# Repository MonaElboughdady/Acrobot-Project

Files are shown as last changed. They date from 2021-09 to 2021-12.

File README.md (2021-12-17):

# Acrobot-Project
The acrobot is a two-link robot manipulator ( it has three links if we counted the base) with only one actuator at the second joint. In this project I designed, and built an acrobot from scratch with the help of my supervisor. we didn't use any motion transfer methods (such as gears and timing belts with pulleys) in this hardware. It was also required to stablize it using LQR control in minimal and maximal coordinates. The mechanical design still needs some modifications for the controller to work in the upright position, but unfortunately I no longer have access to the hardware.  
single pendulum

## The mechanical design and hardware
The design is very simple and the links used are inexpensive and can be obtained easily.To connect the parts together, we designed connections and used 3D printing technology to maufacture them. We designed similar connections that can be produced using milling, but we didn't manufacture them.
### List of components 
this list contains all the mechanical and electronics components that we used (nX) means we used n parts. d = diameter, t= thickness
* Base link: it is a 20mm d X 1mm t X 205mm aluminum tube  https://www.bauhaus.info/metallprofile-kunststoffprofile/kantoflex-rundrohr/p/26683708 (The strength of the tube is good and enough for this application. However, I recommend getting a steel tube for a longer life cycle) 
* Bearings: (2X) 6004-ZZ with width 12mm, Inner diameter 20mm and outer diameter 42mm https://www.bauhaus.info/kugellager/kugellager-6004-zz/p/26538118( you can get other bearings with an inner diameter of 20 mm, but the dimensions of the housing needs to be changed)
* Link1: 1 mm t X 20x20mm X 300mm square Aluminum tube https://www.bauhaus.info/metallprofile-kunststoffprofile/kantoflex-vierkantrohr/p/10508571 
* Link2: it is a 20mm diam* 200mm aluminum tube with a 12mm d X 18 mm steel rod (I recommend getting a 20mm d X 1 mm t X 200mm steel tube or 20mm* 300mm aluminum rod) 
* Motor: Odrive DUAL SHAFT MOTOR D5065 270KV https://eu.odriverobotics.com/shop/odrive-custom-motor-d5065
* Motor driver: ODRIVE V3.6 56volts with connectors https://eu.odriverobotics.com/shop/odrive-v36 ( I may consider getting moteus r4.8 developer kit to build another acrobot but this will require some modifications in the design https://mjbots.com/products/moteus-r4-8-developer-kit )
* Microcontroller: Teensy4.1 development board https://www.conrad.com/p/pjrc-microcontroller-teensy-41-2269230 ( I don't recommend using Arduino microcontroller in this project. You can make it work with arduino however the control code will be more complicated and you will need to use native protocol instead of Ascii for UART communication)
* Encoders: (2X) Incremental capacitive encoder CUI AMT102-V https://eu.odriverobotics.com/shop/cui-amt-102 (I recommend getting absolute encoders as they will reduce the calculations)
* The base:  You can get any wooden or metal base, but you should make sure that it is stable and doesn't move while the acrobot is working)
## Modelling and control
* We used Julia programming language to write the Acrobot parameters, and calculated the LQR controller gains. We also tried to use Julia to control the Acrobot, but it is not a good idea.
(You can also use matlab or any language for calculations)
* We used Arduino IDE to write codes to the teensy. The instructions for installation can be found here https://www.pjrc.com/teensy/td_download.html. You can use both linux and windows operating systems for teensyarduino.
* We ran some experiments on the second actuated link while fixing the first link(simple pendulum). The teensy and Julia codes for the simple pendulum are included in this rep.
## Communication 
Since we need to send torque values to the odrive and receive the positions and velocities data from the odrive, we used UART communication and send the commands using ASCII protocol. More information about ASCII protocol can be found here https://docs.odriverobotics.com/ascii-protocol. I tried testing native protocol. Although it is faster than the ASCII, it is more complicated. You can find more info about the native protocol here https://docs.odriverobotics.com/native-protocol. I have posted my native protocol notes in https://github.com/MonaElboughdady/Acrobot-Project/tree/main/Calculations.

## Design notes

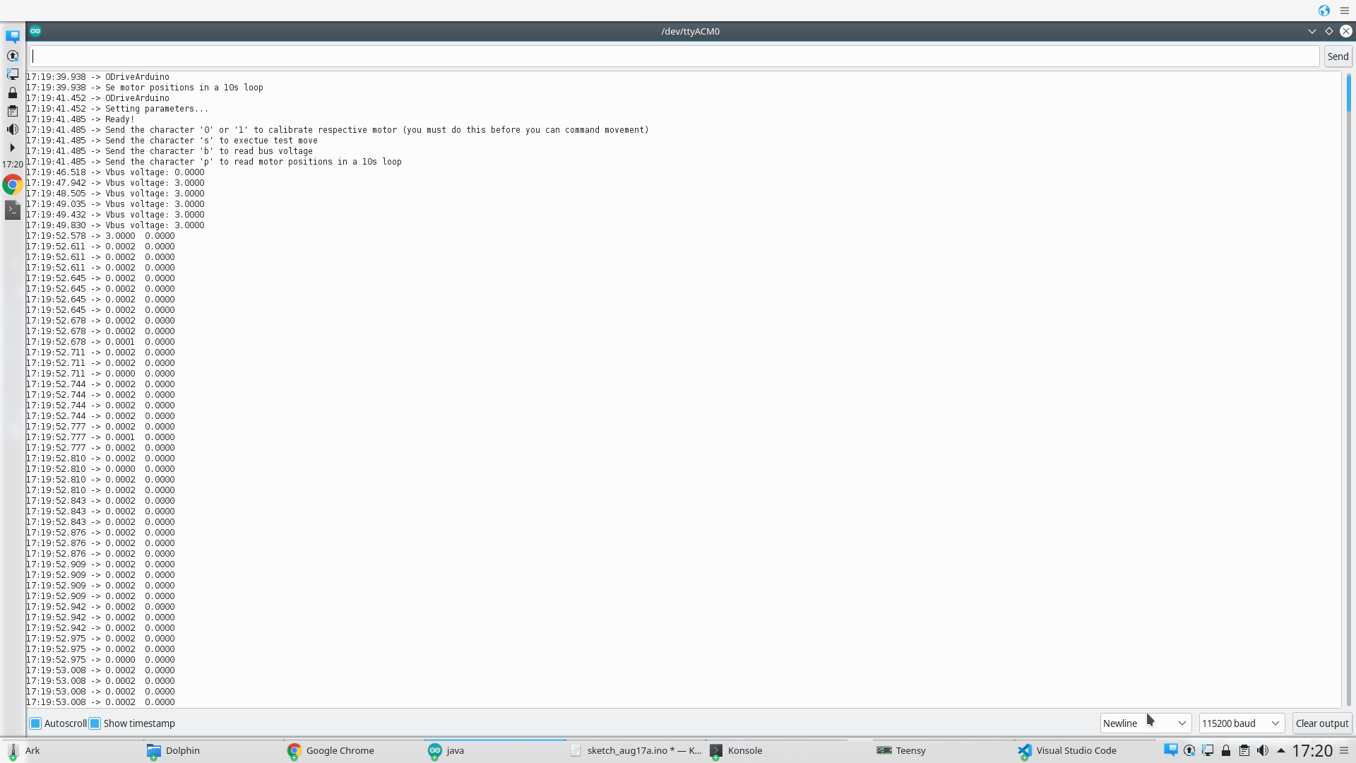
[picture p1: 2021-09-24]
Screenshot_20210924_172021.png

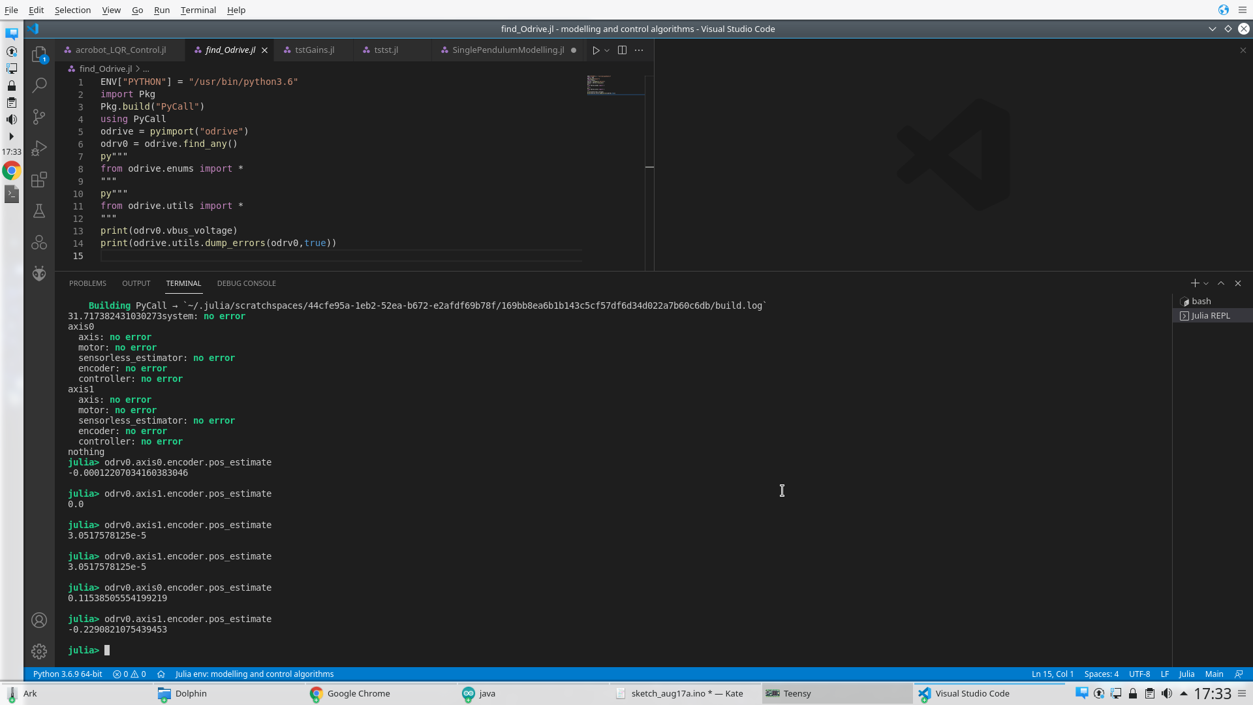
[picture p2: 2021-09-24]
Screenshot_20210924_173316.png

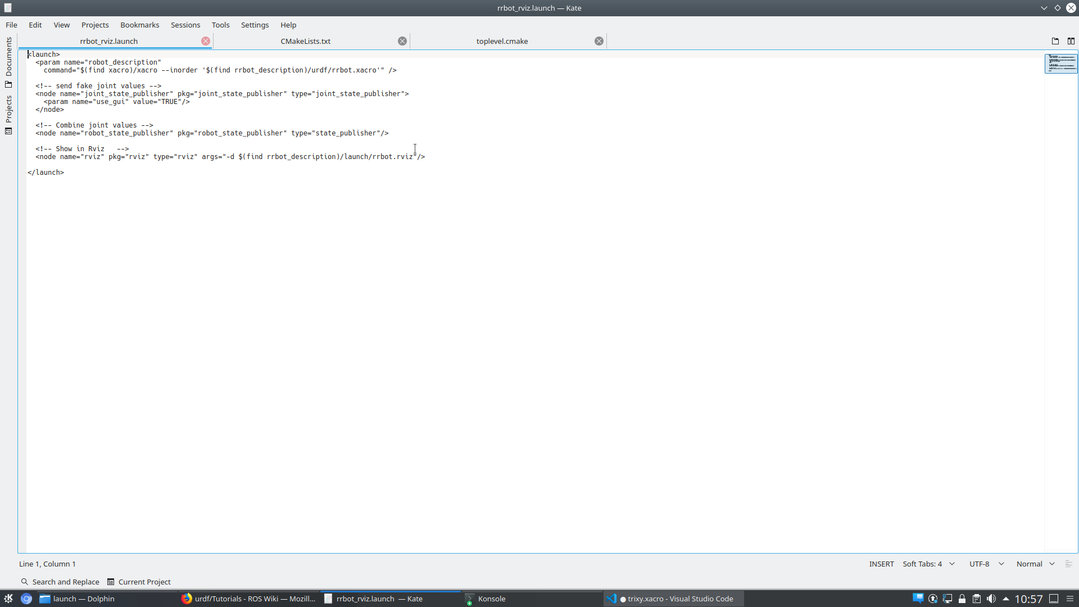
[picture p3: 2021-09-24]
Screenshot_20210520_105743.png

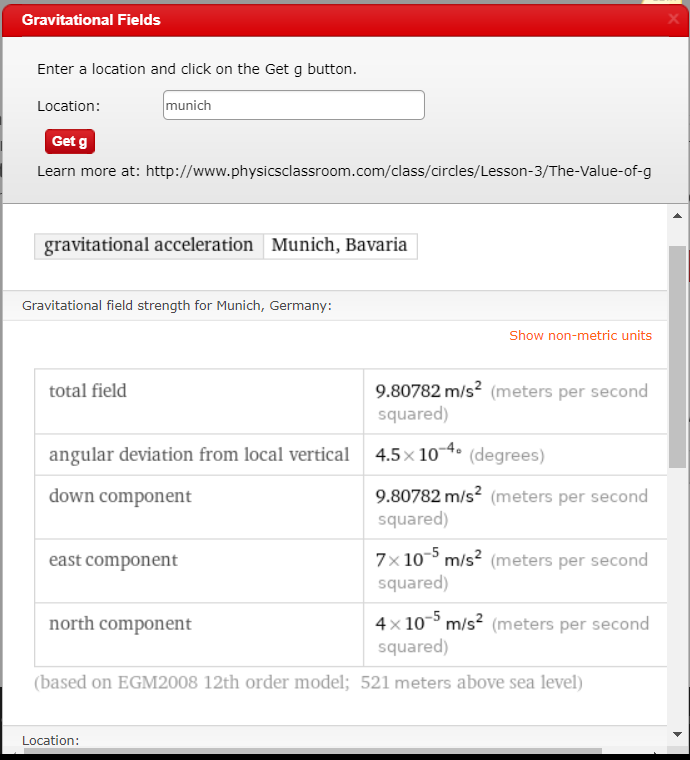
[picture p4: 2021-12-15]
Calculations/GravityInMunich.PNG

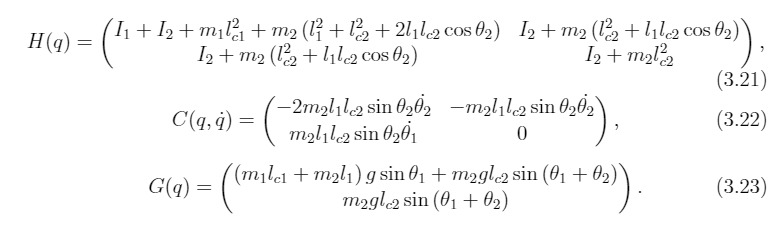
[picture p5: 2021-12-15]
Calculations/WhatsApp Image 2021-10-12 at 3.36.40 PM.jpeg

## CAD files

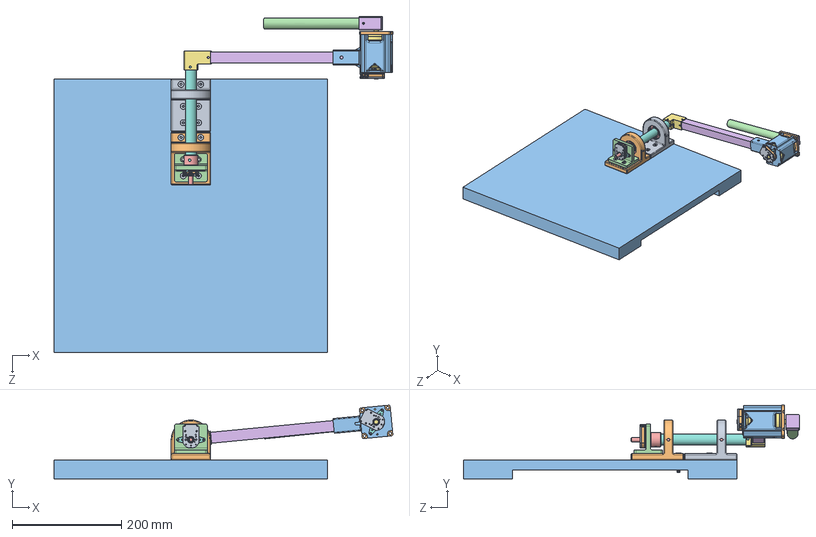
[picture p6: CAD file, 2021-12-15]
Design/Assem1.SLDASM
619.2 x 134.6 x 614.0 mm
base1_left
base1 (1)
enclosure2withrod
Lbracket
connector2
squareCsLink
Motr
amt102-v_01 x 2
amt102-v_02 x 2
amt102-v_03 x 2
amt102-v_04 x 2
amt102-v_05 x 2
amt102-v_06 x 2
amt102-v_07 x 2
amt102-v_08 x 2
amt102-v_09 x 2
amt102-v_10 x 2
amt102-v_11 x 2
amt102-v_12 x 2
amt102-v_13 x 2
amt102-v_14 x 2
amt102-v_15 x 2
AMT-B0-W x 2
hexa csunk highhd screw_iso x 10
enclosure1
woodenBase
Second Link
radial ball bearing_68_din x 2
connectionToRod2_mod
connector_to_base

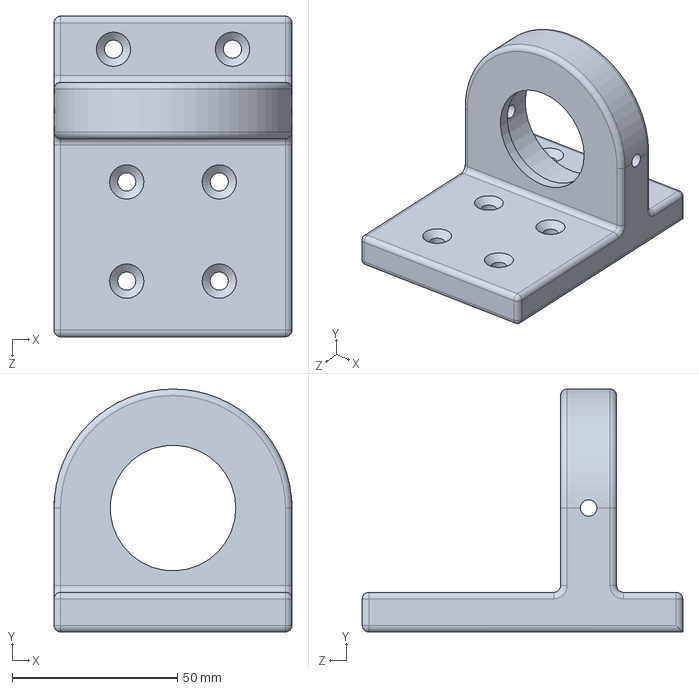
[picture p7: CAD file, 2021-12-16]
Design/base1_left.SLDPRT
72.0 x 73.5 x 97.0 mm

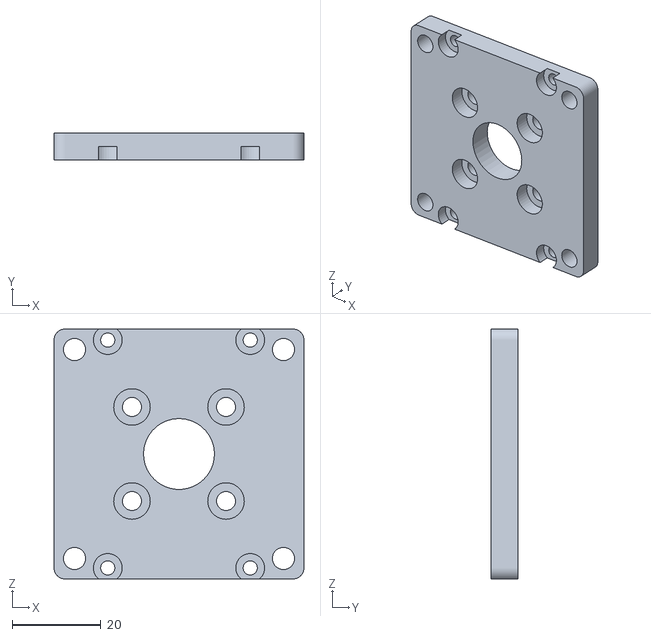
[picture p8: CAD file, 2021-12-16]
Design/STL files/enclosure1.STL
56.4 x 6.00 x 56.4

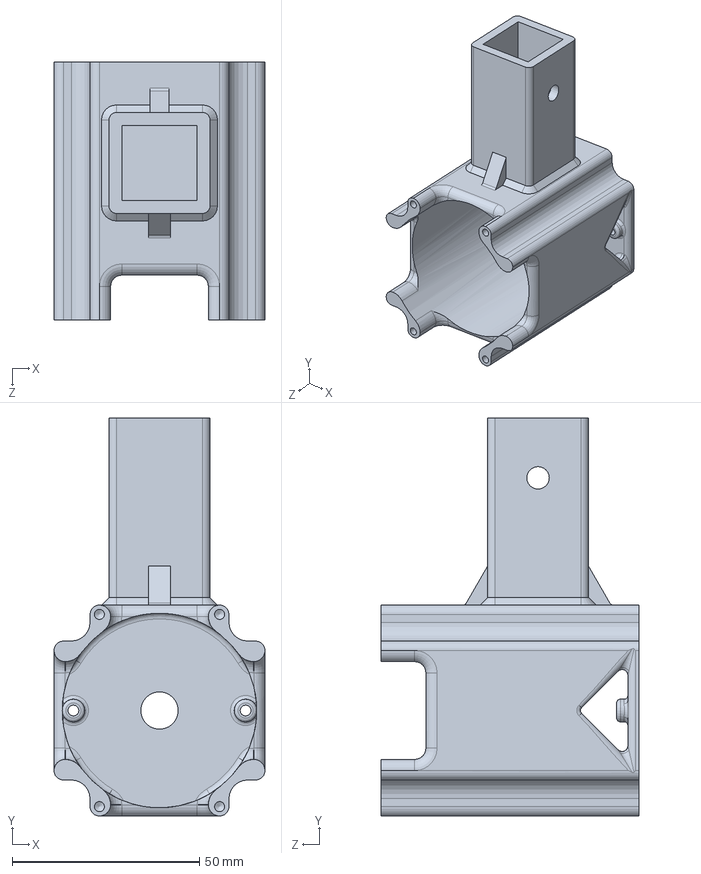
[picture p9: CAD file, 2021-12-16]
Design/enclosure2withrod.SLDPRT
56.4 x 106.4 x 69.0 mm

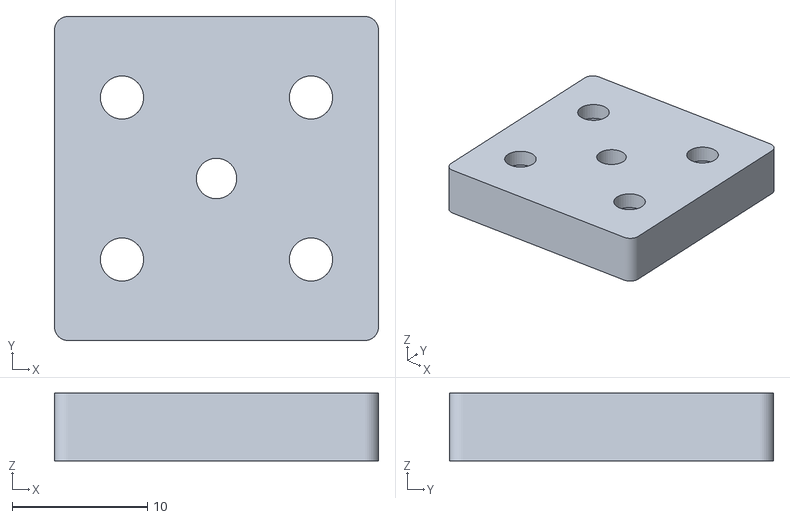
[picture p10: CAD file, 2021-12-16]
Design/STL files/motor_to_link2_p1.STL
24.0 x 24.0 x 5.00

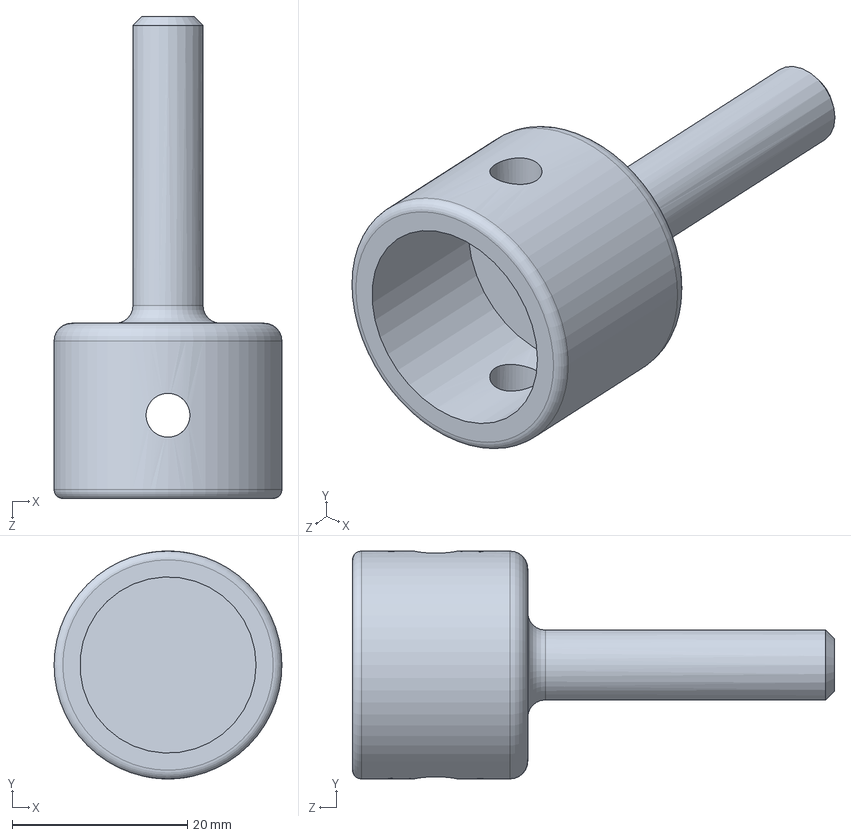
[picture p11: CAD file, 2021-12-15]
Design/connector2.SLDPRT
26.0 x 26.0 x 55.0 mm

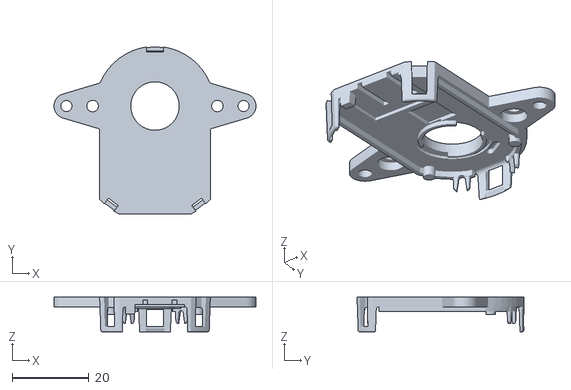
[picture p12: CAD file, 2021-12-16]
Design/STL files/CUI_DEVICES_amt-102-wide-base-rev-j.STL
52.5 x 43.4 x 9.00

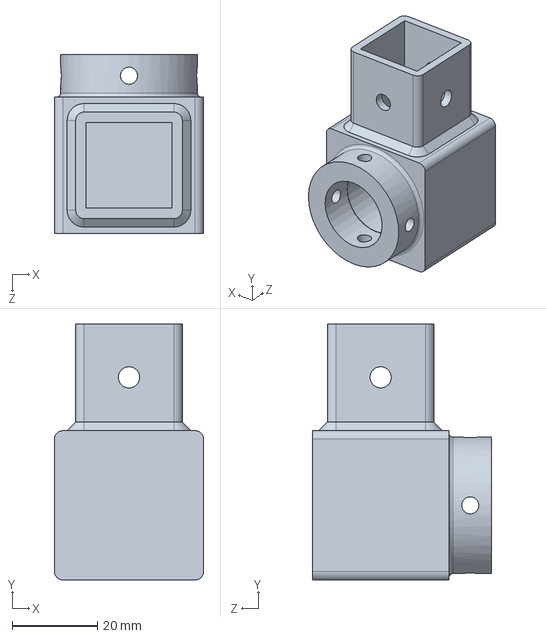
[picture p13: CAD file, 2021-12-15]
Design/connectortolink2.SLDPRT
35.0 x 60.0 x 42.0 mm

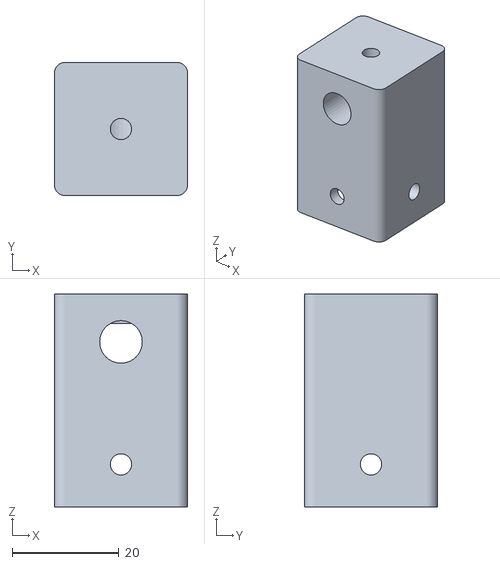
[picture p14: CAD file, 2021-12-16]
Design/STL files/connectionToRod2_mod.STL
25.0 x 25.0 x 40.0

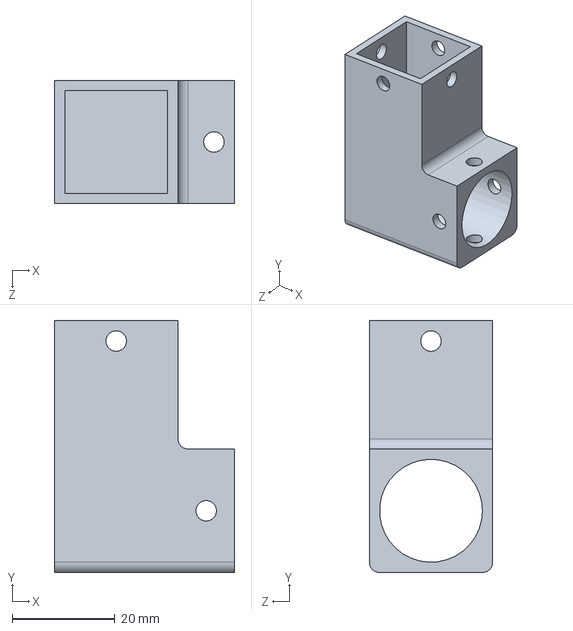
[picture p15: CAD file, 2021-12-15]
Design/connector_to_base.SLDPRT
35.0 x 49.0 x 24.0 mm

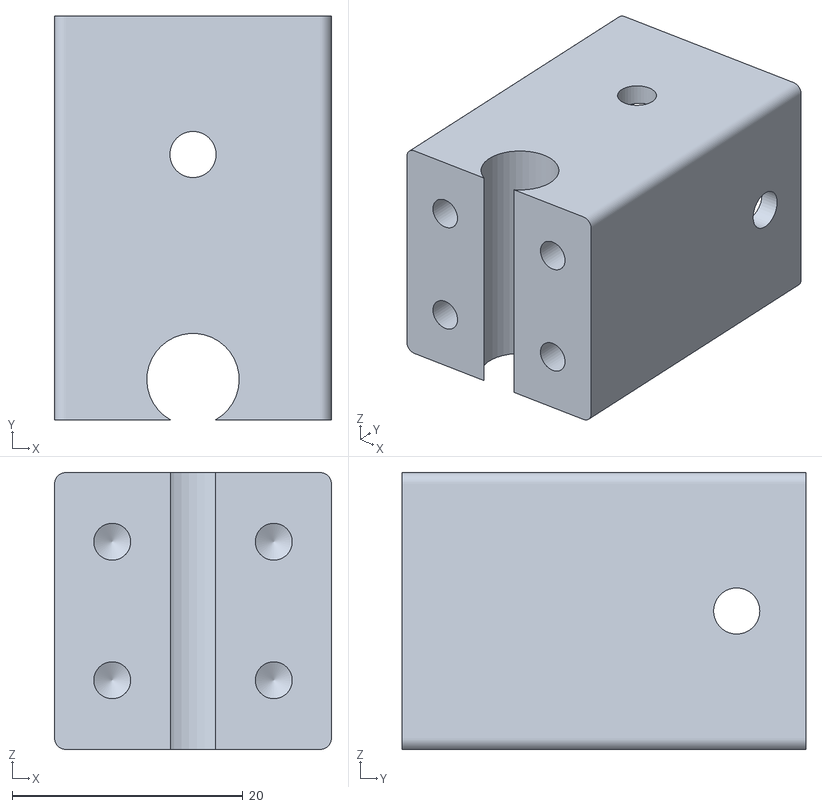
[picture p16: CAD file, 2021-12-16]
Design/STL files/Assem1_motor_connector - motor_to_link2_p2-1.STL
24.0 x 35.0 x 24.0

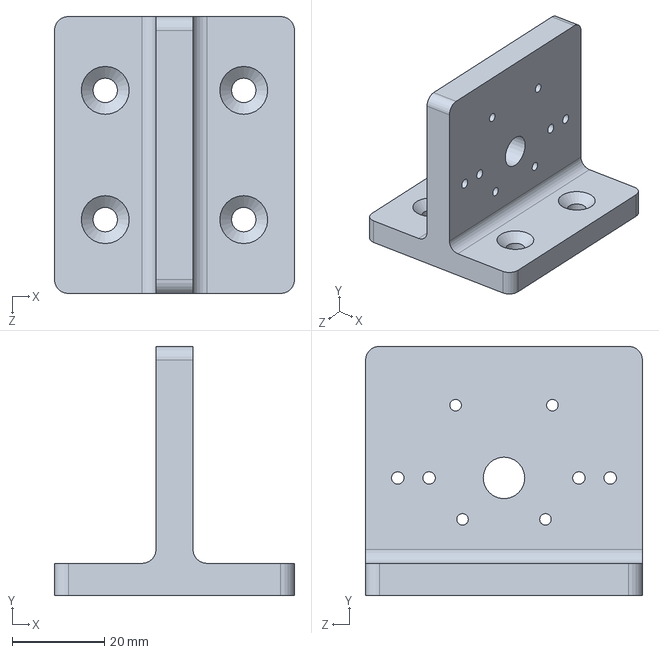
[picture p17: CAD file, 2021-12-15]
Design/Lbracket.SLDPRT
52.0 x 54.0 x 60.0 mm

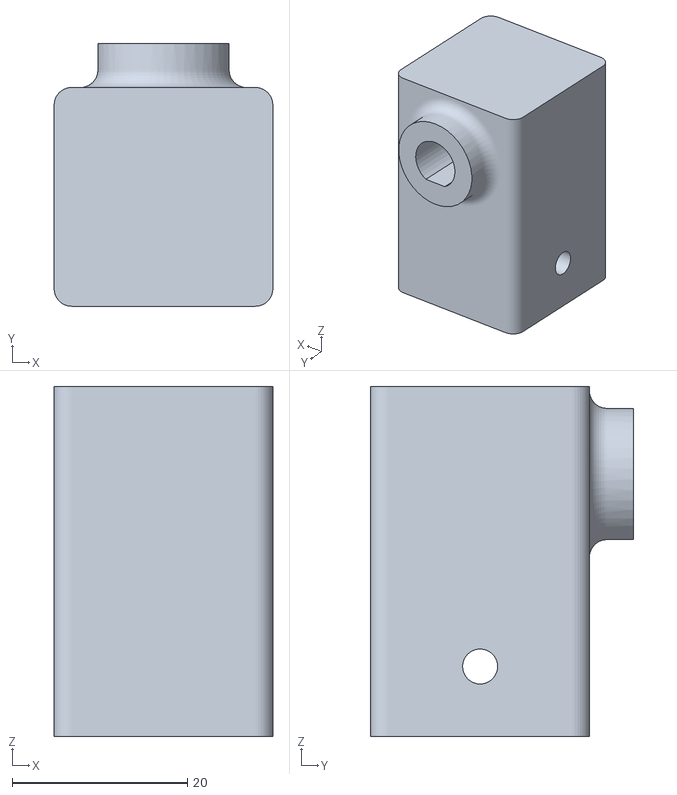
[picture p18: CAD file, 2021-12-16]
Design/STL files/connectionToRod2.STL
25.0 x 30.0 x 40.0

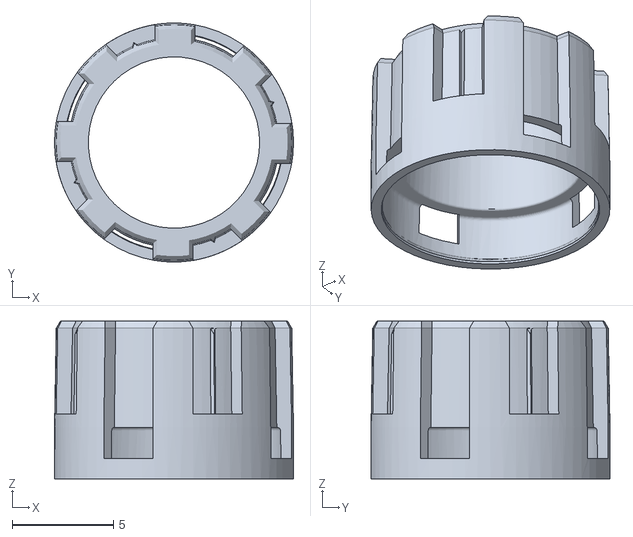
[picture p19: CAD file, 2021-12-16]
Design/STL files/CUI_DEVICES_amt10x-shaft-adaptor-rev-e.STL
11.8 x 11.8 x 7.80

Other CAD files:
Design/STL files/Assem1_motor_connector - motor_to_link2_p1-1.STL
Design/STL files/motor_to_link2_p2.STL
Design/STL files/base1 (1).STL
Design/STL files/Lbracket.STL
Design/STL files/connector2.STL
Design/STL files/connectortolink2.STL
Design/STL files/enclosure2withrod.STL

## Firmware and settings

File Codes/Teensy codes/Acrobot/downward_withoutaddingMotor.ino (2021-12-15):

#include <HardwareSerial.h>
#include <ODriveArduino.h>
#include <math.h>
#include <avr/io.h>

volatile float u, q0, q, dq0, dq, endstopPos, endstopvel;
static uint32_t oldtime;
static uint32_t progtime;
template<class T> inline Print& operator <<(Print &obj,     T arg) {
  obj.print(arg);
  return obj;
}
template<>        inline Print& operator <<(Print &obj, float arg) {
  obj.print(arg, 4);
  return obj;
}

ODriveArduino odrive(Serial1);

void setup()
{ Serial1.begin(921600);
  Serial.begin(921600);
  Serial1.setTimeout(1);
   if (!odrive.run_state(0, 1, false /*don't wait*/)) return;
Serial1 << "c 0" << " " << 0<< "\n";
  while (!Serial) ; /*wait for Teensy Serial Monitor -5.16695  -0.229677  -0.03272  1.0219*/

  Serial1 << "w axis0.controller.config.control_mode 1\n";
  
  Serial1 << "sc" << "\n";
  oldtime = millis();
progtime = millis();
  /*closed loop control*/
//if (!odrive.run_state(0, 8, false /*don't wait*/)) return;
  /*axis state idle*/
  // if (!odrive.run_state(0, 1, false /*don't wait*/)) return;
  //Serial << Serial1.readString() << "\n";
  Serial1.clear();
  u= 0;


}
/*helper for getting the offset*/
int i = 0;
/**/
float   offset1;
float   offset2 ;

/*Control gains       */
//static float l1 = -8.77003;  /*Bryson*/     
//static float l2 = 0.975133;
//static float l3 = 0.982186;
//static float l4 = 0.393173;
//
static float l1 = -1.61576;/*Q=10 R=1**/
static float l2 = -0.143523;
static float l3 = -0.00623429 ;
static float l4 = 0.324385;

static float l1 = -19.7332;/*same maximal*/
static float l2 = 7.69556;
static float l3 = 4.84155 ;
static float l4 = 1.30125;
//static float l1 = -2.29589;
//static float l2 = -0.165354;
//static float l3 = -0.0122479 ;
//static float l4 = 0.457796;

//static float l1 = -3.88;       
//static float l2 = 0.863;
//static float l3 = 0.847;
//static float l4 = 0.174;  
    
//static float l1 = -6.38852;Bryson's
//static float l2 =1.59481;
//static float l3 = 1.4832;
//static float l4 = 0.284831;

//-1.63859  0.0445174  0.0280187  0.322441

//static float l1 = -1.63735 ;/*Q = I, R = 10*/
//static float l2 =0.0420334 ;
//static float l3 = 0.0279742;
//static float l4 = 0.322487;

//static float l1 = -25.01;
//static float l2 =1.84 ;
//static float l3 = 3.64;
//static float l4 = 0.53;
static float l1 = -12.173;/*same maximal weighta*/
static float l2 =9.13344;
static float l3 =5.5163;
static float l4 =0.805554;
void loop()
{
if(!Serial){
   if (!odrive.run_state(0, 1, false /*don't wait*/)) return;
        Serial1 << "c 0" << " " << 0<< "\n";
  }
 if ((millis() - progtime) < 60000) {
  if ( (millis() - oldtime) > 10) {

    if (i == 0) {/*take the offset at the start of the loop and send a  zero torque*/
      oldtime = millis();

      Serial1 << "f 0\n";

      String c1 = Serial1.readString();
 //      Serial << "f0  " << c1 << "\n";

      String placholder = "!";

      c1  = placholder.concat(c1);
      int myspace = 0;
      for (int i = 8; i < 11; i++) {
        if (c1.charAt(i) == ' ') {
          myspace = i;
          break;
        }
      }

      offset1 = (c1.substring(1, myspace)).toFloat();
      endstopvel  = (c1.substring(myspace + 1)).toFloat();

      //      Serial << "p " << offset1 << "\n";

      Serial1 << "f 1 \n";
      myspace = 0;

      String c2 = Serial1.readString();

      String placholder2 = "!";

      c2  = placholder2.concat(c2);

      for (int i = 8; i < 11; i++) {
        if (c2.charAt(i) == ' ') {
          myspace = i;
          break;
        }
      }

      offset2 = (c2.substring(1, myspace)).toFloat();
      endstopvel  = (c2.substring(myspace + 1)).toFloat();

      //      Serial << "p1 " << offset2 << "\n";
      i++;
      Serial1 << "c 0 0" << "\n";
      //      Serial << "The Acrobot is ready!";
    }
    else {
      oldtime = millis();

      Serial1 << "f 0\n";

      String c1 = Serial1.readString();
      //      Serial << "f0  " << c1 << "\n";

      String placholder = "!";
      c1  = placholder.concat(c1);
      int myspace = 0;
      for (int i = 8; i < 11; i++) {
        if (c1.charAt(i) == ' ') {
          myspace = i;
          break;
        }
      }

      q = (c1.substring(1, myspace)).toFloat();
      q = get_angle(offset1, q);
      dq  = ((c1.substring(myspace + 1)).toFloat()) * 2 * PI;
  Serial.print(',');
      Serial.print(q,4);
      Serial.print(',');
      Serial.print(dq,4);
      //      Serial << "p " << q << "\n";
      //      Serial << "v  " << dq << "\n";

      Serial1 << "f 1 \n";
      myspace = 0;

      String c2 = Serial1.readString();
      //Serial << "f1  " << c2 << "\n";

      String placholder2 = "!";
      c2  = placholder2.concat(c2);
      for (int i = 8; i < 11; i++) {
        if (c2.charAt(i) == ' ') {
          myspace = i;
          break;
        }
      }

      q0 = (c2.substring(1, myspace)).toFloat();
      q0 = get_angle(offset2, q0);
      dq0  = ((c2.substring(myspace + 1)).toFloat()) * 2 * PI;
      Serial.print(',');
      Serial.print(q0,4);
      Serial.print(',');
      Serial.print(dq0,4);
      /*Calculate the torque and send it to the odrive*/
      u = (l1 * q0 + l2 * q + l3 * dq0 + l4 * dq) * -0.2;
//      if (u > 1.8 || u < -1.8) {
//        if (!odrive.run_state(0, 1, false /*don't wait*/)) return;
//        Serial1 << "c 0" << " " << 0<< "\n";
//      }
  // Serial1 << "c 0" << " " << u << "\n";
      //
      //      Serial << "p1 " << q0 << "\n";
      //      Serial << "v1  " << dq0 << "\n";
      //      Serial << "Torque: " << u << "\n";
      Serial.print(',');
      Serial.println(u,4);

    }

  }
 }
 else{
    if (!odrive.run_state(0, 1, false /*don't wait*/)) return;
        Serial1 << "c 0" << " " << 0<< "\n";
  }
}
/*Adjusting the angle*/
float get_angle(float ref, float val)
{
  ref = ref - trunc(ref);
  val = val - trunc(val);
  if (ref < 0) {
    ref = ref + 1.0;
  }
  if (val < 0) {
    val = val + 1.0;
  }
  float diff = val - ref;
  if (diff > 0.5) {
    diff = diff - 1.0;
  }
  else if (diff < -0.5) {
    diff = diff + 1.0;
  }
  return diff * 2 * PI;
}

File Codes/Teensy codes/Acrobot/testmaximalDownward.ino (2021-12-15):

#include <HardwareSerial.h>
#include <ODriveArduino.h>
#include <math.h>
#include <avr/io.h>

volatile float u, q1, q2, dq1, dq2;
volatile float px1, px2, py2;
volatile float vx1, vx2, vy1, vy2;
volatile float py1;
static uint32_t oldtime;
static uint32_t progtime;
template<class T> inline Print& operator <<(Print &obj,     T arg) {
  obj.print(arg);
  return obj;
}
template<>        inline Print& operator <<(Print &obj, float arg) {
  obj.print(arg, 4);
  return obj;
}
ODriveArduino odrive(Serial1);
//0.0  -260.321  0.0  0.0  0.0669964  0.0  85.6119  0.0  0.0  0.0467555  0.0  0.0  0.0  -25.4533  0.0  0.0  2.62058  0.0  7.38782  0.0  0.0  0.0835332  0.0  0.0
//0.0  -161.513  0.0  0.0  6.46237  0.0  -1.0467  0.0  0.0  0.0794028  0.0  0.0  0.0  32.5986  0.0  0.0  9.28337  0.0  8.98766  0.0  0.0  0.143635  0.0  0.0
//static float ly1 = -161.513; static float lz1 = 0.0; static float lvy1 = 6.46237  ; static float lvz1 =  0.0; static float l1/*ltx1*/ =  -1.0467; static float l3/*lwx1*/ = 0.0794028;
//static float ly2 = 32.5986; static float lz2 = 0.0; static float lvy2 = 9.28337; static float lvz2 = 0.0; static float l2/*ltx2*/ = 8.98766; static float l4/*lwx2*/ = 0.143635;
//static float ly1 =-260.321; static float lz1 = 0.0; static float lvy1 =0.0669964  ; static float lvz1 =  0.0; static float l1/*ltx1*/ = 85.6119 ; static float l3/*lwx1*/ =  0.0467555;
//static float ly2 = -25.4533 ; static float lz2 = 0.0; static float lvy2 = 2.62058; static float lvz2 = 0.0; static float l2/*ltx2*/ = 7.38782; static float l4/*lwx2*/ =   0.0835332;
//static float ly1 =-99.4308; static float lz1 = 0.0; static float lvy1 =1.72413 ; static float lvz1 =  0.0; static float l1/*ltx1*/ = 36.2608 ; static float l3/*lwx1*/ =  0.0427897;
//static float ly2 = 13.0616 ; static float lz2 = 0.0; static float lvy2 = 2.43281; static float lvz2 = 0.0; static float l2/*ltx2*/ = 0.33327; static float l4/*lwx2*/ = 0.0487164;
static float ly1 =-105.41; static float lz1 = 0.0; static float lvy1 =8.64147 ; static float lvz1 =  0.0; static float l1/*ltx1*/ = -1.834 ; static float l3/*lwx1*/ =  0.117364;
static float ly2 = 58.7459 ; static float lz2 = 0.0; static float lvy2 = 7.18558; static float lvz2 = 0.0; static float l2/*ltx2*/ = 5.26996; static float l4/*lwx2*/ = 0.101116;
float ref1 = -0.1625;
float ref2 = -(0.325 + 0.1);

void setup() {
  // put your setup code here, to run once:
  Serial1.begin(921600);
  Serial.begin(921600);
  Serial1.setTimeout(1);
  Serial1 << "c 0 0" << "\n";
  if (!odrive.run_state(0, 1, false /*don't wait*/)) return;
  Serial1 << "sc" << "\n";

  while (!Serial) ; /*wait for Teensy Serial Monitor*/
  /*torque control mode*/
  Serial1 << "w axis0.controller.config.control_mode 1\n";
  /*clear errors*/
  Serial1 << "sc" << "\n";
  oldtime = millis();
  progtime = millis();
  /*closed loop control*/
  if (!odrive.run_state(0, 8, false /*don't wait*/)) return;
  Serial1.clear();
}
/*helper for getting the offsets*/
int i = 0;
/*define the offsets*/
float   offset1 = 0.0303650;//these are the index offsets of the encoders, the readings are done agaain in the loop as we cant make that the first encoder return to the index offset as axis 1 is not actuated
float   offset2 = -0.001007;
void loop() {
  // put your main code here, to run repeatedly:
   if ((millis() - progtime) < 60000) {
  if (!Serial) {
    /*when existing the serial monitor the acrobot stops*/
    Serial1 << "c 0 0" << "\n";
    if (!odrive.run_state(0, 1, false /*don't wait*/)) return;
  }
  else {
    
    if ( (millis() - oldtime) > 10) {
      if (i == 0) {
        oldtime = millis();

        Serial1 << "f 0\n";
        String c1 = Serial1.readString();
        String placholder = "!";
        c1  = placholder.concat(c1);
        int myspace = 0;

        for (int i = 8; i < 11; i++) {
          if (c1.charAt(i) == ' ') {
            myspace = i;
            break;
          }
        }

        offset2 = (c1.substring(1, myspace)).toFloat();

        Serial1 << "f 1 \n";
        myspace = 0;
        String c2 = Serial1.readString();
        String placholder2 = "!";
        c2  = placholder2.concat(c2);

        for (int i = 8; i < 11; i++) {
          if (c2.charAt(i) == ' ') {
            myspace = i;
            break;
          }
        }

        offset1 = (c2.substring(1, myspace)).toFloat();

        i++;
        u = 0;

        Serial1 << "c 0 0" << "\n";

        px1 = 0.0;
        px2 = 0.0;
        py1 = 0.1625;
        py2 = 0.425;

      }
      else {
        oldtime = millis();

        Serial1 << "f 1 \n";
        int myspace = 0;
        String c2 = Serial1.readString();
        String placholder2 = "!";
        c2  = placholder2.concat(c2);

        for (int i = 8; i < 11; i++) {
          if (c2.charAt(i) == ' ') {
            myspace = i;
            break;
          }
        }


        q1 = (c2.substring(1, myspace)).toFloat();
        q1 = get_angle(offset1, q1);
        dq1  = ((c2.substring(myspace + 1)).toFloat()) * 2 * PI;
        px1 =  0.1625 * sinf(q1);
        //py1 = -0.1625 * cosf(q1);
        vx1 =  0.1625 * cosf(q1) * dq1;
        //vy1 =  0.1625 * sinf(q1) * dq1;
        Serial.print(',');
        Serial.print(q1);
        Serial.print(',');
        Serial.print(dq1);
        Serial.print(',');
        Serial1 << "f 0\n";

        String c1 = Serial1.readString();
        String placholder = "!";
        c1  = placholder.concat(c1);
        myspace = 0;

        for (int i = 8; i < 11; i++) {
          if (c1.charAt(i) == ' ') {
            myspace = i;
            break;
          }
        }

        q2 = (c1.substring(1, myspace)).toFloat();
        q2 = get_angle(offset2, q2);
        dq2  = ((c1.substring(myspace + 1)).toFloat()) * 2 * PI;
        px2 =  0.10 * sinf(q1 + q2) + 0.325 * sinf(q1);
        //py2 = -0.10 * cosf(q1 + q2) - 0.325 * cosf(q1);
        vx2 =  0.10 * cosf(q1 + q2) * (dq1 + dq2) + 0.325 * cosf(q1) * dq1;
        // vy2 =  0.10 * sinf(q1 + q2) * (dq1 + dq2) + 0.325 * sinf(q1) * dq1;

        Serial.print(q2);
        Serial.print(',');
        Serial.print(dq2);
        Serial.print(',');
        // u = (l1 * q1 + l2 * q2 + l3 * dq1 + l4 * dq2 + ly1 * (px1) + ly2 * (px2) + lz1 * (py1 + 0.1625) + lz2 * (py2 + 0.425) + lvy1 * (vx1) + lvy2 * (vx2) + lvz1 * (vy1) + lvz2 * (vy2)) * -1;
       u = (l1 * q1 + l2 * q2 + l3 * dq1 + l4 * dq2 + ly1 * (px1) + ly2 * (px2) + lvy1 * (vx1) + lvy2 * (vx2) ) * -0.2;
       Serial1 << "c 0" << " " << u << "\n";

        Serial.println(u);
      }

    }

  }
   }
 else{
    if (!odrive.run_state(0, 1, false /*don't wait*/)) return;
        Serial1 << "c 0" << " " << 0<< "\n";
  }
}
float get_angle(float ref, float val)
{
  ref = ref - trunc(ref);
  val = val - trunc(val);
  if (ref < 0) {
    ref = ref + 1.0;
  }
  if (val < 0) {
    val = val + 1.0;
  }
  float diff = val - ref;
  if (diff > 0.5) {
    diff = diff - 1.0;
  }
  else if (diff < -0.5) {
    diff = diff + 1.0;
  }
  return diff * 2 * PI;
}

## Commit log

2021-09-23 Create 3D printed Parts
2021-12-15 Decoded Odrive Native protocol
    I will provide an organized version of this file soon
2021-12-15 The final encoder base
    The encoder base can be manufactured using 3D printing or milling. It is suitable for the AMT102 encoder.
    [Lbracket.SLDPRT]
2021-12-15 The full assembly
    this may not work, so check the zip file
    [Assem1.SLDASM]
2021-12-15 connects base link to link1
    This is the milled part design
    [connector_to_base.SLDPRT]
2021-12-15 connects base link to link 1
    maufactured by 3D priniting
    [connectortolink2.SLDPRT]
2021-12-15 the base link extension shaft
    The reason behind the extension is that we couldn't find a 20mm to 8mm coupler. This can be manufactured using 3D printing or turning
    [connector2.SLDPRT]
2021-12-16 The motor enclosure body
    I have added a square tube to be able to fix the square tube aluminum rod. You can find the original file here https://discourse.odriverobotics.com/t/nema-enclosures-for-d5065-and-d6374-motors/830
    [enclosure2withrod.SLDPRT]
2021-12-16 Bearing housing
    [base1_left.SLDPRT]
2021-12-16 Create STL files for 3D printing
